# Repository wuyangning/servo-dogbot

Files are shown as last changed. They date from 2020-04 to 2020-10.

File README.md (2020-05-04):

# puppy-bot


视频演示：https://www.bilibili.com/video/BV1if4y1U7h3
# 文件目录
- cad(step)
    - step模型文件
- puppy_bot
    - 源码，使用platformio
- sim5link
    - 简易的5杆机构运动学仿真

# 关于
- 为了把电池塞进去，由原来的12个舵机改成了8个。舵机也直接由单片机驱动。
- 通过修改一些参数就可以切换各种步态，但不是所有步态都能用。这取决于舵机的性能。测试中trot步态是效果最好的。
- 目前只有一个陀螺仪，可以适应不同坡度的平面地形。其他的复杂的地面，落差小一点还可以。
- 五杆机构惯量小，布局起来也很方便。但是非线性比较严重，在一些位置受力和精度会很差。
- 用的是纯位置控制(非常原始的控制方法)。目前只完成步态和一些动作的验证。完整的控制流程和一些保护机制还需要慢慢添加。仅作参考😂。大概流程如下。



# 使用
- 目前是直接用pwm输出给舵机，用的陀螺仪是串口陀螺仪GY952。如果是其他舵机驱动方式或陀螺仪。需要在myimu中先实现欧拉角的输出，在myservo中实现关节角的输出。
- 舵机需要标定，这一步比较麻烦(之后弄个上位机)。舵机脉宽和关节角的之间是一个线性关系，需要在myservo.h中确定。每条腿的连杆和关节角的定义如下(关节角是连杆以绿线为起点，逆时针旋转的角度)：

- 参数
```C
//LF,RB,RF,LB的步态相位
float phase[4]={0,0,0.5,0.5}
//腿悬空时的平均速度(mm/us)
//太小会导致轨迹失真，太大不能保证步态
float flight_speed=0.0003; 
//轨迹参数
//有两种轨迹可选，椭圆或两段直线
struct trajy_para
{
    float flight_period; //腿腾空的周期占比(1-占空比)
    uint8 trajy_type; //滞空的轨迹类型 1为椭圆轨迹，0为两段直线
    float tx; //腿的目标位置
    float tz;
    float hx; //抬腿的最高位置
    float hz; //如果是椭圆轨迹，表示椭圆半短轴
    uint8 num_talbe;//存入的轨迹表

};
```
- 调用或切换步态的流程
```C
//相位
phase[4]={0,0,0.5,0.5};
//生成轨迹存入轨迹表
trajy_para param={0.5,1,40,0,20,20,0};
trajy_planning(param);
//每条腿通过三段直线轨迹由当前位置过渡到新步态的初始位置
//两个参数分别是过渡时的步态(0:trot,1:walk)和抬腿高度
gait_transit(0,20);

void loop() 
{
    //循环执行轨迹表
    gait_loop();
}

```

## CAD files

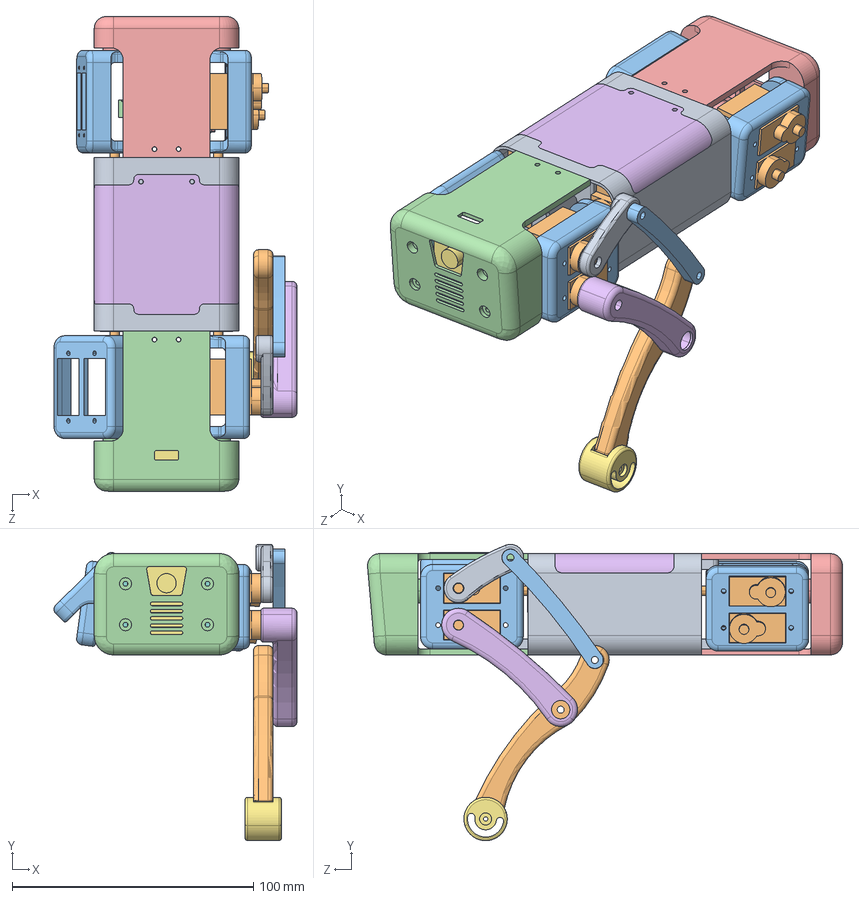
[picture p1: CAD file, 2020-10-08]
cad(step)/new-puppy-bot12.STEP
100.8 x 122.9 x 197.0 mm
嗆儂 x 8
嗆儂殤 x 4
head
β
奻裔
k210
ヶ啣
牷旋1
苤虯
嶺裝
JST - XH - Thru (V) - 3Pin - 2.54mm
XT30_Stecker
大腿s - 副本
foot

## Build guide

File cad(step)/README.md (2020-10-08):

- pupppy-bot12是最早的12舵机版本，预留的空间比较少，放不下太多东西。

- puppy-bot8是后面修改的8舵机版本，有更大的空间，细节也更完善。可以直接内置两节18650(建议使用动力18650)。

- new-puppy-bot12新画的12舵机版本

- 舵机尺寸是标准的9g。建议使用数字舵机，速度不低于0.1s/60°。

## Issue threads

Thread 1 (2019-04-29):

关于控制器

XCMB, 2019-04-29:
Arduino Maple在淘宝没有搜到，可否给个链接。另外Maple是可以接入ArduinoIDE的吗？感谢！

YANGGTT, 2019-05-03:
用stm32就可以了，搜arduino+stm32关键词就有了

XCMB, 2019-05-03:
我最后买了mega，关于3d打印你有遇到过法兰轴承的安装部分特别容易断开吗，就是打印层与层之间不结实，横向用力就会在截面断开。

YANGGTT, 2019-05-05:
> 我最后买了mega，关于3d打印你有遇到过法兰轴承的安装部分特别容易断开吗，就是打印层与层之间不结实，横向用力就会在截面断开。

这个是会的，结构设计不合理，装轴承的地方太薄了，不要强装就不容易断了

XCMB, 2019-05-08:
我给你开洞穿了个螺丝

XCMB, 2019-05-08:
我给她穿洞开了个螺丝

zenithcheung, 2019-08-09:
老铁， 你代码：  //绑定各个舵机到，pwm扩展板上的引脚
  leg_lf.servo_attach(8,9,11,1);
  leg_lb.servo_attach(4,5,7,0);
  leg_rf.servo_attach(12,13,15,1);
  leg_rb.servo_attach(0,1,3,0);

其中， 8，9，11 对应是哪个关节呢？ 8是肩部么？ 后面的 1 是代表方向对吧，
之后的， 4，，， 12，   0， 是分别哪个腿呢？

YANGGTT, 2019-08-10:
是的

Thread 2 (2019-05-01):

5v10A-20A 稳压求型号

harry32009, 2019-05-01:
大大怎么处理mg996的电压问题？7.4v锂电池直接供电嘛？还是用了大功率dc-dc？求型号求方案

YANGGTT, 2019-05-03:
用的是12v-5v的dc-dc，淘宝有卖的

XCMB, 2019-05-03:
如果你有自己焊接电路的能力的话可以试一下芯片mp2482,可提供5V@5A的供电

harry32009, 2019-05-03:
哈哈，

淘宝买了XL4005模块，4片，打算一条腿三路舵机一片，不知道够不够

------------------ 原始邮件 ------------------
发件人: "XCMB"<notifications@github.com>;
发送时间: 2019年5月3日(星期五) 下午2:59
收件人: "YANGGTT/spotmicro-controller"<spotmicro-controller@noreply.github.com>;
抄送: "洪隆樟"<717699998@qq.com>; "Author"<author@noreply.github.com>;
主题: Re: [YANGGTT/spotmicro-controller] 5v10A-20A 稳压求型号 (#2)

如果你有自己焊接电路的能力的话可以试一下芯片mp2482,可提供5V@5A的供电

&mdash;
You are receiving this because you authored the thread.
Reply to this email directly, view it on GitHub, or mute the thread.

wskongdesheng, 2019-07-07:
大神能不能留个联系方式，我也在研究spotmicro那个，我的微信是wskongdesheng, 邮箱是wskongdesheng@163.com

zhuwei, 2019-12-13:
请教下。我也想研究运动学，应该看哪些书？

YANGGTT, 2019-12-16:
> 请教下。我也想研究运动学，应该看哪些书？

可以从蔡自兴的机器人学看起

zhuwei, 2019-12-17:
@YANGGTT 非常感谢。近期准备整一套这个机器狗。能否加个方式，向你学习下。

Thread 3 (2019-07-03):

请问有9g servo版本的那只狗狗的图纸源文件吗？

hyansuper, 2019-07-03:
我基于ROS写了个T站的那只狗狗的仿真，github.com/hyansuper/spotmicro，实现了两种步态，主要思路是根据速度指令预测下一个落脚点然后抬起一只脚，同时根据步子的节奏移动重心到另外三只支撑脚构成的平面内。步子看起来还算自然。其他形式的步态有空还会研究。
我还没打印实体机器人，我也担心996 servo扭矩不足。

你的9g servo版本的小狗看起来会更灵活，不知你有没有它活动的视屏可分享，另外，我想将我的spotmicro项目用于这个9g servo版本的小狗，你是否愿意分享设计源文件呢（Solidworks 或 Fusion360的格式）这样如果我需要修改尺寸会更方便。谢谢！

YANGGTT, 2019-07-07:
第一个文件夹里的puppy-bot.STEP就是设计源文件。这个我还没动起来，没时间做了。腿是5杆机构，处理起来可能比较麻烦。

hyansuper, 2019-07-08:
你用的是塑料齿轮的蓝色舵机吗？请问舵机转子和连杆打印件怎么固定在一起？

Closed 2019-07-13.

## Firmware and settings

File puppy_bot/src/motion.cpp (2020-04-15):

#include "motion.h"


KINE leg[4];
PID ROLL,PITCH;


//LF,RB,RF,LB的步态相位
float phase[4]={0.0,0.0,0.5,0.5}; 
//轨迹表，储存坐标和延迟（速度信息）
float trajy_table[trajy_table_num][trajy_table_size][2]; 
//滞空的平均速度(mm/us)，舵机响应速度越高越接近真实速度
float flight_speed=0.0003; 

//以固定时间间隔执行轨迹表中的点
int point_time;
int period_points;

const unsigned int sample_time=20;
unsigned long current,lastime;


extern void get_rpy();

 
void setup_motion()
{
    init_servo();
    init_imu();

    leg[LF].servo_attach(6,7);
    leg[LB].servo_attach(3,2);
    leg[RF].servo_attach(4,5);
    leg[RB].servo_attach(1,0);

    leg[LF].set_pose(-10,-80);
    leg[LB].set_pose(-30,-80);
    leg[RF].set_pose(-10,-80);
    leg[RB].set_pose(-30,-80);

    for(int i=0;i<4;i++)
    {
        leg[i].spx=leg[i].cx;
        leg[i].spz=leg[i].cz;
        leg[i].table=0;
    }

    ROLL.set_pid(0.02,0.0,0.02,20,0.1);
    PITCH.set_pid(0.03,0.0,0.02,20,0.1);

    ROLL.target=0;
    PITCH.target=0;

} 

void trajy_planning(trajy_para p) 
{
    //滞空为半椭圆轨迹或两段直线
    //直线轨迹是匀速的，椭圆轨迹可以获得一定加减速效果

    period_points=int(flight_points/p.flight_period);
    int prop_points=period_points-flight_points;

    if(p.trajy_type)
    {
        float a=sqrt(p.tx*p.tx+p.tz*p.tz)/2; //椭圆半长轴
        float theta;
        float phi=atan2(p.tz,p.tx);

        for(int i=0;i<flight_points;i++)
        {
            theta=PI-i*PI/flight_points;
            trajy_table[p.num_talbe][i][X]=
                a*cos(theta)*cos(phi)-p.hz*sin(theta)*sin(phi)+p.tx/2;
            trajy_table[p.num_talbe][i][Z]=
                a*cos(theta)*sin(phi)+p.hz*sin(theta)*cos(phi)+p.tz/2;
        }
        point_time=int((PI*p.hz+2*(a-p.hz))/(flight_speed*flight_points));
    }
    else
    {
        float s1=sqrt(p.hx*p.hx+p.hz*p.hz);
        float s2=sqrt(pow(p.tx-p.hx,2)+pow(p.tz-p.hz,2));
        int lift_points=int((s1*flight_points)/(s1+s2));
        int drop_points=flight_points-lift_points;

        float delta_lx=p.hx/lift_points;
        float delta_lz=p.hz/lift_points;
        float delta_dx=(p.tx-p.hx)/drop_points;
        float delta_dz=(p.tz-p.hz)/drop_points;

        for(int i=0;i<lift_points;i++)
        {
            trajy_table[p.num_talbe][i][X]=delta_lx*i;
            trajy_table[p.num_talbe][i][Z]=delta_lz*i;
        }
        for(int i=0;i<drop_points;i++)
        {
            trajy_table[p.num_talbe][i+lift_points][X]=delta_dx*i+p.hx;
            trajy_table[p.num_talbe][i+lift_points][Z]=delta_dz*i+p.hz;
        }

        point_time=int((s1+s2)/(flight_speed*flight_points));
    }
    

    //支撑轨迹为直线

    float delta_px=-p.tx/prop_points;
    float delta_pz=-p.tz/prop_points;

    for(int i=0;i<prop_points;i++)
    {
        trajy_table[p.num_talbe][i+flight_points][X]=delta_px*i+p.tx;
        trajy_table[p.num_talbe][i+flight_points][Z]=delta_pz*i+p.tz;
    }

}

void gait_loop()
{
    int ps[4];
    for(int i=0;i<period_points;i++)
    {
        for(int j=0;j<4;j++)
        {
            ps[j]=i+int(phase[j]*period_points);
            if(ps[j]>=period_points)
                ps[j]-=period_points;
            leg[j].set_pose(trajy_table[leg[j].table][ps[j]][X]+leg[j].spx,trajy_table[leg[j].table][ps[j]][Z]+leg[j].spz);

        }
	
		//在支撑相调整机器人(测试中)
		/*
        if((i>0.25*period_points&&i<0.5*period_points)||(i>0.75*period_points&&i<period_points))
        {
                get_rpy();
                ROLL.compute();
                PITCH.compute();
                rotation_platform(ROLL.output,PITCH.output);
                lastime=current;

                leg[LF].spz+=(-ROLL.output+PITCH.output);
                leg[RF].spz+=(ROLL.output+PITCH.output);
                leg[LB].spz+=(-ROLL.output-PITCH.output);
                leg[RB].spz+=(ROLL.output-PITCH.output);

        }
		*/

        delayMicroseconds(point_time);
    }

}

void gait_transit(uint8 type,float lift_height)
{
    //通过三段直线由当前位置过渡到步态的初始位置
    //待改进

    uint8 points=int(flight_points/3); //每段直线的插补点数
       
    float delta_x[4]; //x方向的增量
    float delta_dz[4]; //落腿时z方向的增量
    int pt[4];//点之间时间
    float delta_lz=lift_height/points;//抬腿时z方向的增量

    for(uint8 i=0;i<4;i++)
    {
        delta_x[i]=(trajy_table[leg[i].table][int(phase[i]*period_points)][X]
            +leg[i].spx-leg[i].cx)/points;
        delta_dz[i]=(trajy_table[leg[i].table][int(phase[i]*period_points)][Z]
            +leg[i].spz-leg[i].cz-lift_height)/points;
        
        pt[i]=int(10*(abs(delta_x[i])+abs(delta_dz[i])+abs(delta_lz))/(flight_speed*flight_points));
        Serial.println(pt[i]);
    }

    if(type) //walk
    {
        for(uint8 i=0;i<4;i++)
        {
            for(uint8 j=0;j<points;j++)
            {
                leg[i].mov(0,delta_lz);
                delayMicroseconds(pt[i]);
            }
            for(uint8 j=0;j<points;j++)
            {
                leg[i].mov(delta_x[i],0);
                delayMicroseconds(pt[i]);
            }
            for(uint8 j=0;j<points;j++)
            {
                leg[i].mov(0,delta_dz[i]);
                delayMicroseconds(pt[i]);
            }
            delay(200);
        }
    }   
    else //trot
    {
        for(uint8 i=0;i<points;i++)
        {
            leg[0].mov(0,delta_lz);
            leg[1].mov(0,delta_lz);
            delayMicroseconds(pt[0]);
        }
        for(uint8 i=0;i<points;i++)
        {
            leg[0].mov(delta_x[0],0);
            leg[1].mov(delta_x[1],0);
            delayMicroseconds(pt[0]);
        }
        for(uint8 i=0;i<points;i++)
        {
            leg[0].mov(0,delta_dz[0]);
            leg[1].mov(0,delta_dz[1]);
            delayMicroseconds(pt[0]);
        }
        delay(200);
        for(uint8 i=0;i<points;i++)
        {
            leg[2].mov(0,delta_lz);
            leg[3].mov(0,delta_lz);
            delayMicroseconds(pt[2]);
        }
        for(uint8 i=0;i<points;i++)
        {
            leg[2].mov(delta_x[2],0);
            leg[3].mov(delta_x[3],0);
            delayMicroseconds(pt[2]);
        }
        for(uint8 i=0;i<points;i++)
        {
            leg[2].mov(0,delta_dz[2]);
            leg[3].mov(0,delta_dz[3]);
            delayMicroseconds(pt[2]);
        }
        delay(200);
    }
      
}

void rotation_platform(float rx,float ry)
{

  leg[LF].mov(0,-rx+ry); 
  leg[RF].mov(0,rx+ry);
  leg[LB].mov(0,-rx-ry); 
  leg[RB].mov(0,rx-ry);
   
}

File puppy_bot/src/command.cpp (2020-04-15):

#include "Arduino.h"
#include "command.h"

char command[64];
byte command_length;

void init_command()
{

  for (byte i=0; i<64; i++)
    command[i] = 0;
  command_length = 0;
}

void cli_loop()
{
  char c;
  while(Serial.available() > 0)
  {
    c = Serial.read();
    if (c != cm_end)
    {
      command[command_length] = c;
      command_length++;
    }
  }
 
  if (command_length && (c == cm_end) )
  {
    process_command();
    init_command();
  }
  
}



/*-----------------------------------------------------------------------------------------*/
void process_command()
{

  byte code = 0;
  
  
  if (command_seen(cm_start) )
  { 
    
    code = (int)key_value(cm_start);
    switch (code)
    {
      
      case 0:
        pwmWrite(servo_num[int(key_value('n'))],int(key_value('p')));
        Serial.println("done");
      break;

    }
   
  }
  

  
  

}
/*-----------------------------------------------------------------------------------------*/


double key_value(char key)
{
  char temp[10] = "";

  for (byte i=0; i<command_length; i++)
  {
    if (command[i] == key)
    {
      i++;      
      int k = 0;
      while (i < command_length && k < 10)
      {
        if (command[i] == cm_sep || command[i] == cm_end)
          break;

        temp[k] = command[i];
        i++;
        k++;
      }
    return strtod(temp, NULL);
    }
  }
  
  return 0;
}


bool command_seen(char key)
{
  for (byte i=0; i<command_length; i++)
  {
    if (command[i] == key)
      return true;
  }
  
  return false;
}

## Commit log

2020-04-15 renamed: puppy-bot/puppy-bot.STEP -> puppy-bot/puppy-bot-12.STEP
    [puppy-bot-12.STEP, puppy-bot.STEP]
2020-04-15 git add .
    [puppy-bot-12.STEP, puppy-bot12.STEP]
2020-10-08 添加新画的12舵机版本
    [new-puppy-bot12.STEP]
2021-03-13 删除旧版的12舵机模型
    [puppy-bot12.STEP]
